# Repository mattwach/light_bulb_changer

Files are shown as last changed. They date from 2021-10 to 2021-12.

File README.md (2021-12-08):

# Light Bulb Changer

_Note: I also made a [video describing the project](https://youtu.be/A-EdzPTZSjM)._

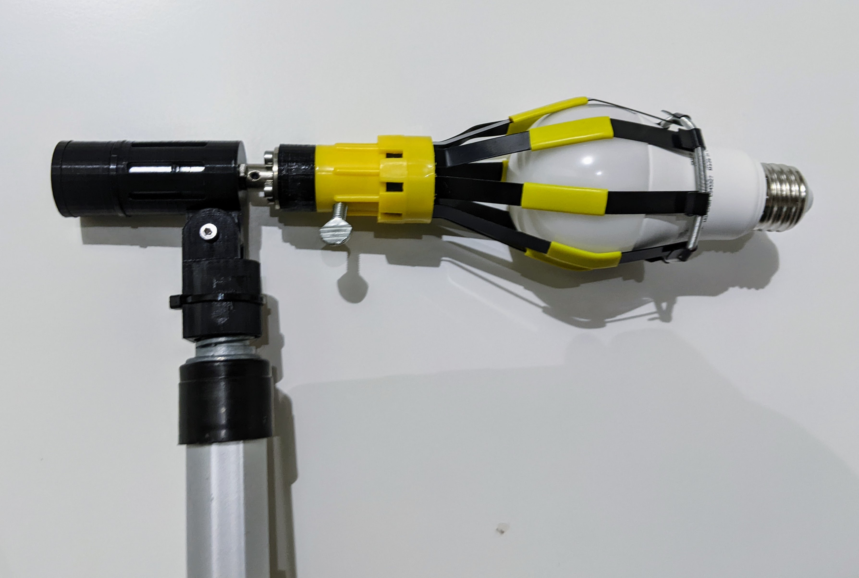
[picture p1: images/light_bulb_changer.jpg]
Light bulb changer


Do you have hard-to-reach light bulbs?  If so, then you are perhaps familiar a
_Light Bulb Changer_.  It threads on the end of a pole and extends your reach. 
A problem is one of mechanics.  If you can't get your pole square to the bulb,
the effectiveness of the holder decreases rapidly.  Imagine trying to use
this thing at a 90 degree angle to the bulb.  That is the exact situation I
found myself in: 

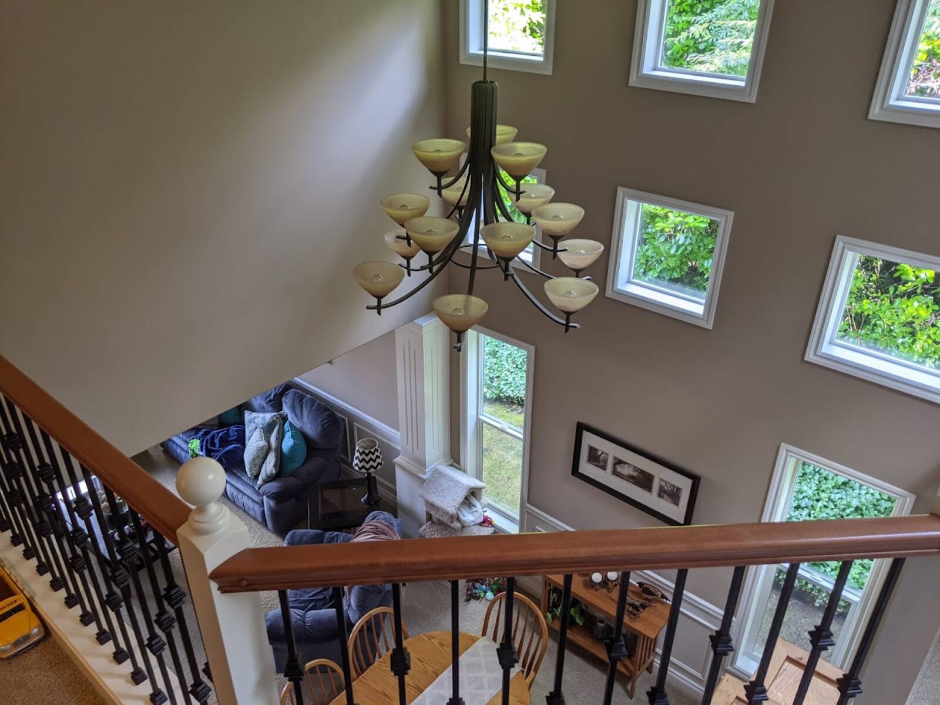
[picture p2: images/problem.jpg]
The Problem


OK. Just get a tall ladder, move that table, make that suspicious call
confirming my life insurance details and up I go.  Just kidding, I instead
used this as an excuse for another maker project.

I spent way more time on this than the ladder would have taken.  Then again, it
was quite a bit of fun and now I have a useful tool on-hand ready to square off
against the next light bulb challenge.  Lucky for you, all of the design,
modeling, and testing steps are done so you can build one in a fraction of the time.
Heck, I even include a walkthrough below.

Of course if you want extra challenge, feel free to mod up the design below to
match your favorite parts and techniques.  Have it play inspirational music, add
Bluetooth for some reason... Your imagination, skill, time and budget are your
only limits.

If you don't have a 3D printer, hope is not lost.  You can always use a project
box, parts from the hardware store and plenty of zip ties to get things done old
school.

## Step 1: Parts

Here is what I built:

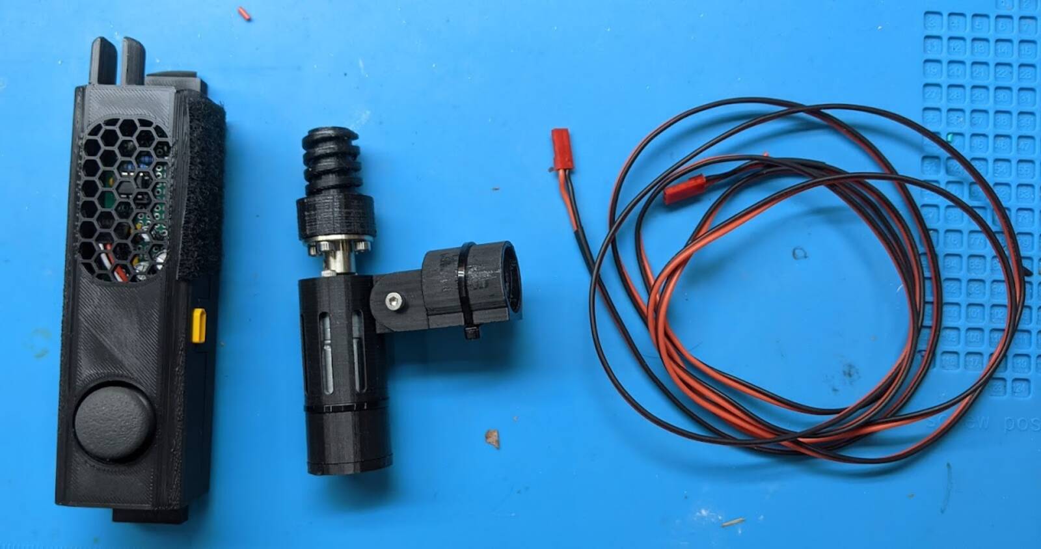
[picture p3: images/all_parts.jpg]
All of the parts


The middle unit is a motorized driver that the light bulb changer screws onto.
It then screws on a pole.  Now you have both a motor and a way to change the
angle.  There is also a control box that goes on the other end of the pole.

### Parts I used include:

   1. **[Geared brushed motor](https://www.amazon.com/gp/product/B0728HDH45)**.  These
      are around $13 on Amazon, probably cheaper other places.  I went with 200
      RPM which is a bit more than 3 rotations/second at 12V.  This seemed about
      right.
   2. **[Flange Coupling Connector](https://smile.amazon.com/gp/product/B07PDYV4P3)**. 
      This is needed to adapt the motor's shaft to the _Light Bulb Changer_.
   3. **Microcontroller**. I went with the [ATTiny85](https://www.sparkfun.com/products/9378)
      Loading firmware on it can be tricky if you have not done so before.  But there are
      dozens of video and written guides on the internet on how to do it.  Once you
      get it working the first time, it will be turn key after that.
   4. **[L293D](https://www.adafruit.com/product/807) H-bridge motor driver**.
      This turns the puny waveforms the ATTiny85 can generate into power boosted
      energy waves that can drive a motor at variable speeds and in either forward
      or reverse.
   5. **Broomstick** for mounting
   6. **[Enough wire](https://www.amazon.com/BNTECHGO-Flexible-Conductor-Resistant-Extension/dp/B077X9MVWG)**
      to reach all the way down the broomstick.
   7. **Zipties** to secure the control module to the broomstick.
   8. **[Sony PS2 thumbstick](https://www.amazon.com/HiLetgo-Controller-JoyStick-Breakout-Arduino/dp/B00P7QBGD2)**
      which is basically a thumb-friendly potentiometer. Any 10k potentiometer will work,
      so long as you can handle the ergonomics.
   9. **A power source**.  You'll need around 12V and enough current to keep the motor
      happy.  A [3S lipo battery](https://www.amazon.com/TATTU-Battery-650mAh-Torrent-Lizard/dp/B071GBGBB4)
      (450-1800 mAh) fits this bill perfectly, but you'll need a special charger if you don't already
      have one.  You can also stack 9 (or more) AA batteries in series.  A 12V DC wall wart could also work.
   10. **Connectors for the power source**.  With a small 3S LIPO, I really like
       the [XT30 connector](https://www.amazon.com/10Pairs-Upgrade-Connector-Female-Battery/dp/B08P5HVMYT)
       and that is what the 3D printed case is designed to handle without
       "manual modifications"
   11. **PCB prototyping board** - Technically optional as there are so many way to construct a circuit.
       But a [30x70 perf board](https://www.amazon.com/ELEGOO-Prototype-Soldering-Compatible-Arduino/dp/B072Z7Y19F)
       is my personal preference.
   12. **Status LED(s)**.  I went with a two-color LED which has red and green
       channels.  You can also go with two separate LEDs of any color you want with minimal changes.
   13. **Some current limiting resistors** for the LEDs.  Values are not critical -
       something in the 470 to 2k range will work.
   14. **A 5V regulator**.  I went with the LP2950Z but [nearly anything](https://www.sparkfun.com/products/107)
       will work here. 
   15. **Some capacitors**.  The DC motor is a noisy load for the battery and the 5V
       regulator will see this noise on it's input.  Caps on each side of the
       regulator will help reduce this noise to the 5V electronics  I went with
       500+ uF on the input side and another 100 uF on the output side, which is
       likely overkill.
   16. **Connectors** for the PS2 thumbstick and motor wire.  I used standard 2.54mm pitch
       headers.  Anything you have could work.

### Tools you'll need:

   1. **A 3D printer** if you want print the motor housing and controller box.  As
      said above, you can also come up with a custom alternate solution.
   2. **A Breadboard** if you want to verify operation before committing the parts with
      solder.

## Step 2: Electronics Overview

The ordering is not strict here but I like getting the electronics working
first.  A breadboard is a good way to wire things up and some confidence
that the project is on the right track.

Here is the schematic:

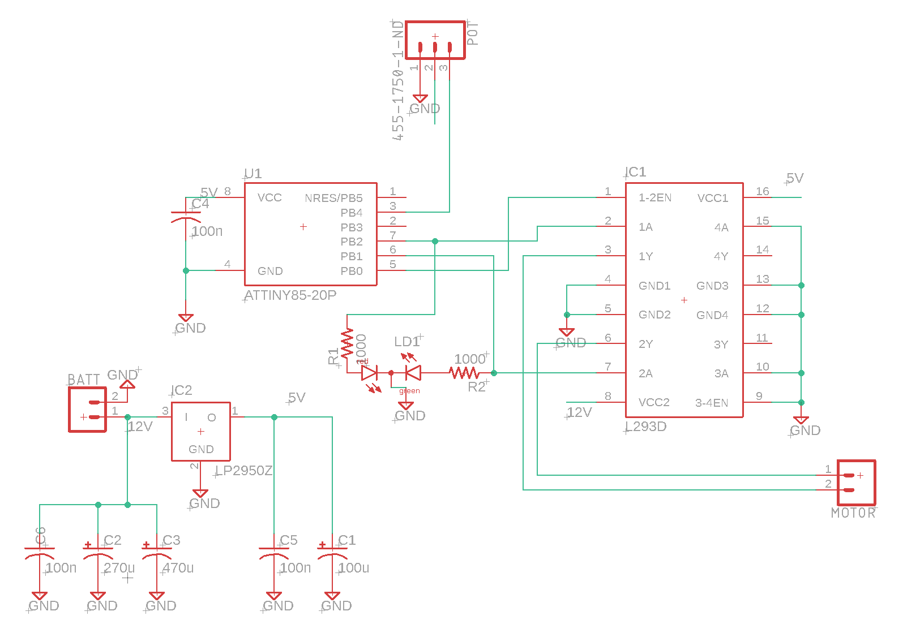
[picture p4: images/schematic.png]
Schematic


You do not need to starting wiring up the breadboard yet, as upcoming steps
will break that down into smaller steps

So how does this thing work?

   * You move the potentiometer (PS2 thumbstick, top of schematic)
   * The ATTiny85 microcontroller notes the new potentiometer state (via `PB4`)
     and uses it to update the motor direction and speed. 
   * The direction and speed are communicated via a PWM signal (via `PB0`) which
     tells the motor how fast to spin via the only language it understands: power.
     The microcontroller also sends a signal (via PB1 and PB2) that tells the motor
     controller which polarity to send to the motor.
   * The L293D motor controller (right) takes the weak PWM signal from the microcontroller and
     puts the full force of the battery pack behind it (e.g. 12V and whatever
     current the motor asks for - within obvious limits..)
   * The bottom left of the circuit is just the 5V regulator and some supporting
     capacitors to filter out motor noise.

You can probably imagine the rest - adapter on motor, light bulb changer on
adapter and light.  Turning, problems being solved, happy time.

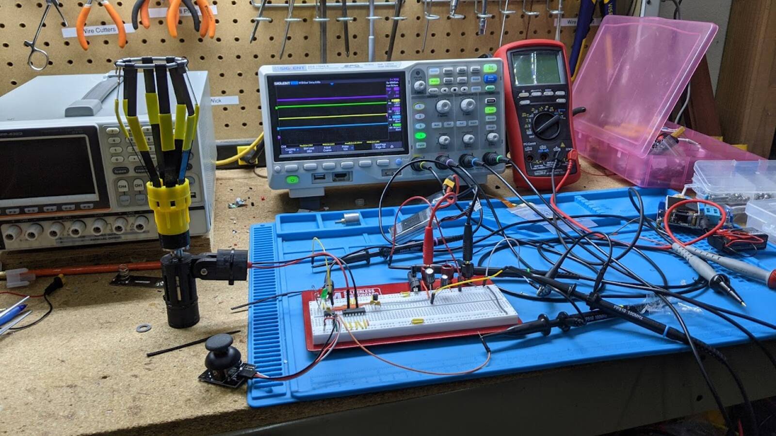
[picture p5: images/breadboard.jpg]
Breadboard


## Step 3: ATTiny85 Programming and Testing

The code is located in the `firmware/` directory.  This code is not Arduino so
you will need to have/develop familiarity with `avr-gcc` to compile it.  But,
**you don't have to compile it** because there is an already-compiled
`firmware/prebuilt/light_bulb_changer.hex` file ready to go.

Loading code onto the ATTiny85 involves conforming to the protocol specified in
its
[datasheet](https://ww1.microchip.com/downloads/en/DeviceDoc/Atmel-2586-AVR-8-bit-Microcontroller-ATtiny25-ATtiny45-ATtiny85_Datasheet.pdf).
There are several possible solutions and a large amount of websites and Youtube
videos that cover the topic.

A sampling of options include:

   1. The official AVR programming tools
   2. [Using an Arduino Uno (or nano) *as a programmer*](https://create.arduino.cc/projecthub/arjun/programming-attiny85-with-arduino-uno-afb829)
   3. [Using the Sparkfun ATTiny85 programmer](https://learn.sparkfun.com/tutorials/tiny-avr-programmer-hookup-guide/all)

I personally went with a variation of option #2, using an Arduino Nano and
a [test clip](https://www.amazon.com/Pomona-Electronics-5250-Plated-Spacing/dp/B00JJ4G13I):

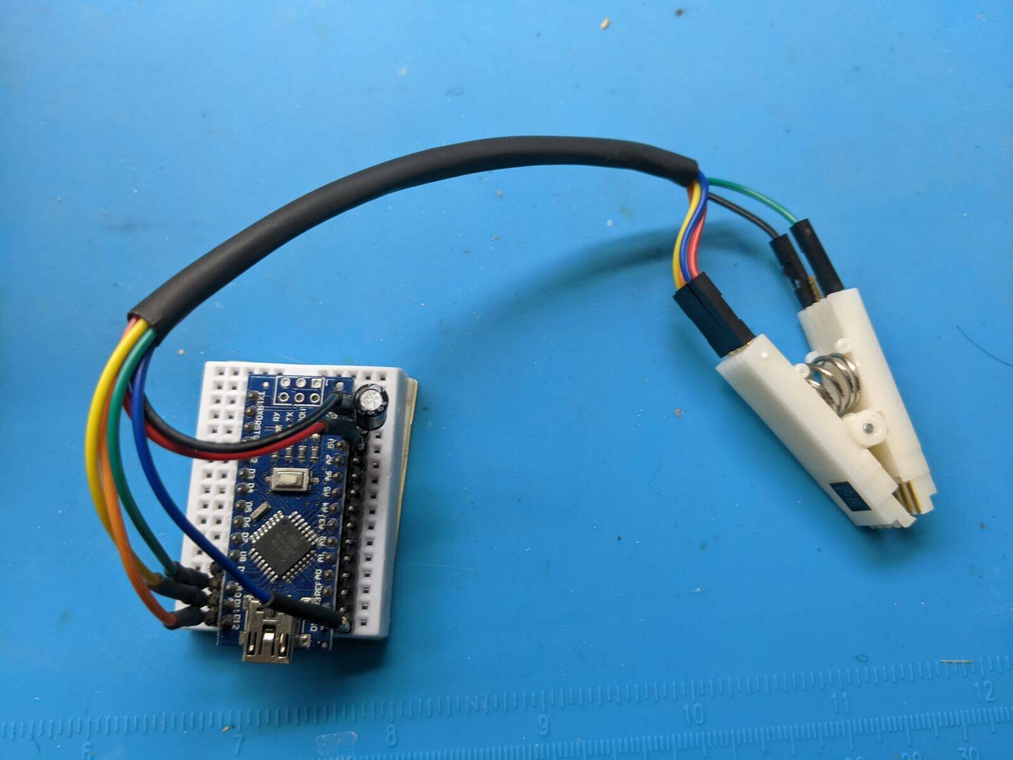
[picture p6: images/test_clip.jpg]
Test Clip


The three guides I listed above assume that you want to use the Arduino framework to
_write code_ for the ATTiny85.  Maybe you do, but Arduino can not compile the code here
and you already have a compiled `light_bulb_changer.hex` file ready to upload so compiling
it again is not needed.

Still it's convenient to follow the steps because as a part of the exercise,
you'll end up with a copy of the
[avrdude](https://www.nongnu.org/avrdude/) code uploading tool as well as
examples of how to use it.

When you run the "blinking light" example of one of the guides above, the
Arduino console will output the `avrdude` command it used.  This can be compared
to the one I used (which is also in `firmware/prebuilt/README`):

    # in the firmware/prebuilt directory:

    /usr/bin/avrdude \
      -C./avrdude.conf \
      -v \
      -pattiny85 \
      -cstk500v1 \
      -P /dev/ttyUSB0 \
      -b19200 \
      -Uflash:w:light_bulb_changer.hex:i

Depending on the programming tools you have and the OS you
are using, some flags will be different and you'll want to combine the
flags from the blinking light example with the `-Uflash:w:light_bulb_changer.hex:i`
option above.

OK, now that we are through all of that, I suggest a simple verification on the
breadboard.  We will wire up a simplified version of the schematic as shown:

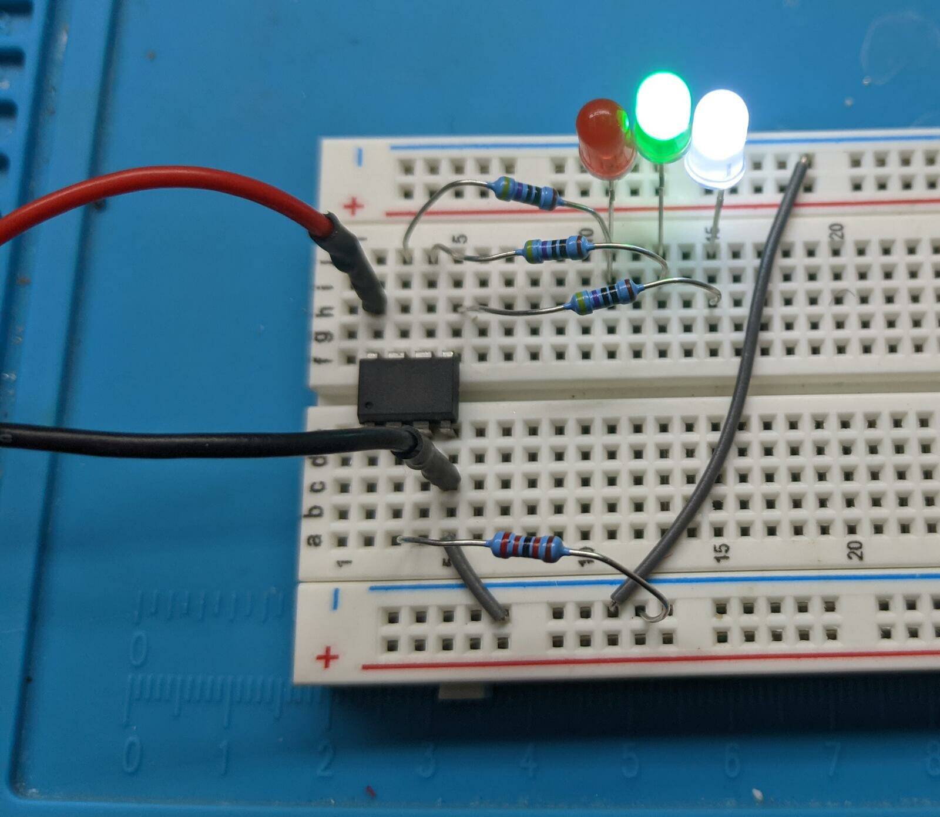
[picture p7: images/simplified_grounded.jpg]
Simplified Grounded Breadboard


This follows the original schematic but with the motor enable (pin 1 of the
    L293D) replaced with a white LED and the potentiometer replaced with a
resistor to ground.  Specifically:

   * Pin 1 (Reset) Not Connected
   * Pin 2 (Pot input) -> Resistor -> Ground
   * Pin 3 Not Connected
   * Pin 4 (`GND`) -> Ground
   * Pin 5 (`PWM`) -> Resistor -> White LED -> Ground
   * Pin 6 (Forward) -> Resistor -> Greed LED -> Ground
   * Pin 7 (Reverse) -> Resistor -> Red LED -> Ground
   * Pin 8 (5V) -> Some voltage between 2V-5.5V

What resistor values?  Anything in the 400-5K range is fine for the LEDs.
Anything at all is fine for Pin 2.

What we should see is the green and white LEDs lit up.  The firmware thinks that
the motor is in full-power forward mode because we have Pin 2 grounded.

Now lets, make one change.  Instead of grounding Pin 2, connect it to power:

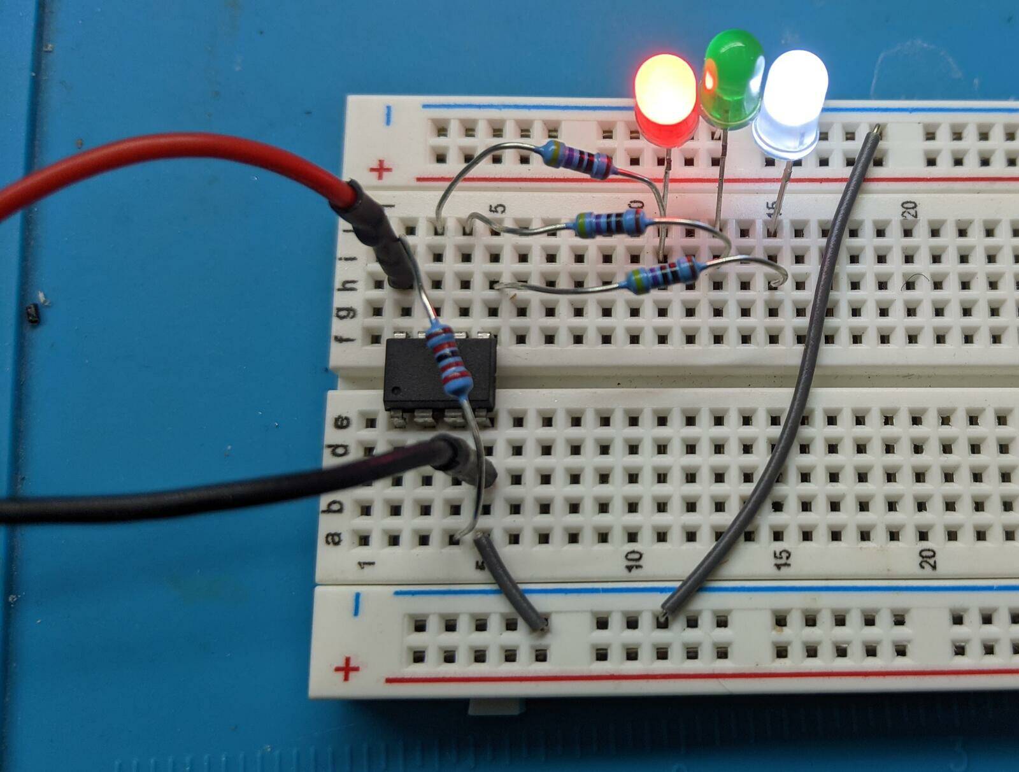
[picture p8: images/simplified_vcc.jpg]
Simplified VCC Breadboard


Now the ATTiny85 thinks it need to drive the motor full power in reverse.

You could call the testing "done" at this point, but I'm going to take it a
little further for educational purposes.  Here I connected a real potentiometer
to pin 2 (I didn't go with the PS2 thumbstick just yet because I wanted to
    potentiometer to stay at a certain value for the test).  I also added
an oscilloscope probe to pin 5:

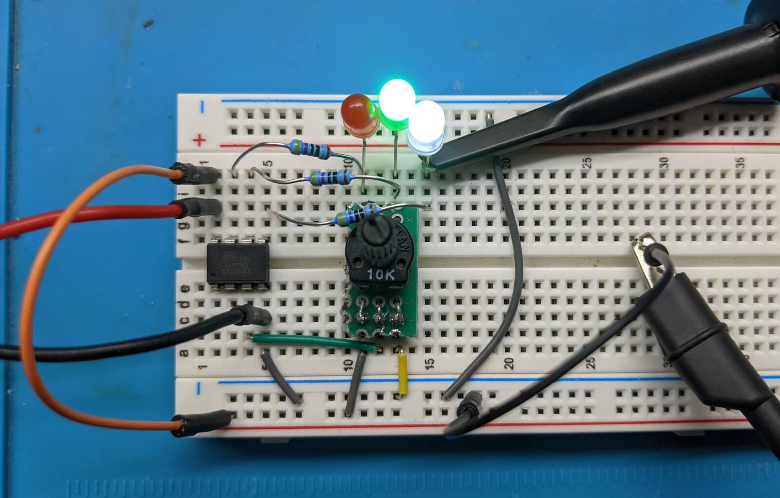
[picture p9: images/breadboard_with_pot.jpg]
Breadboard with Potentiometer


Now the potentiometer can be used to change between forward and reverse, just
like the final product.  It's also possible to see the white LED getting
darker and brighter but this is more obvious from the oscilloscope.  Here
is a scope image at "low power", where the motor will turn more slowly.  Note
how the signal spends most of it's time at 0V:

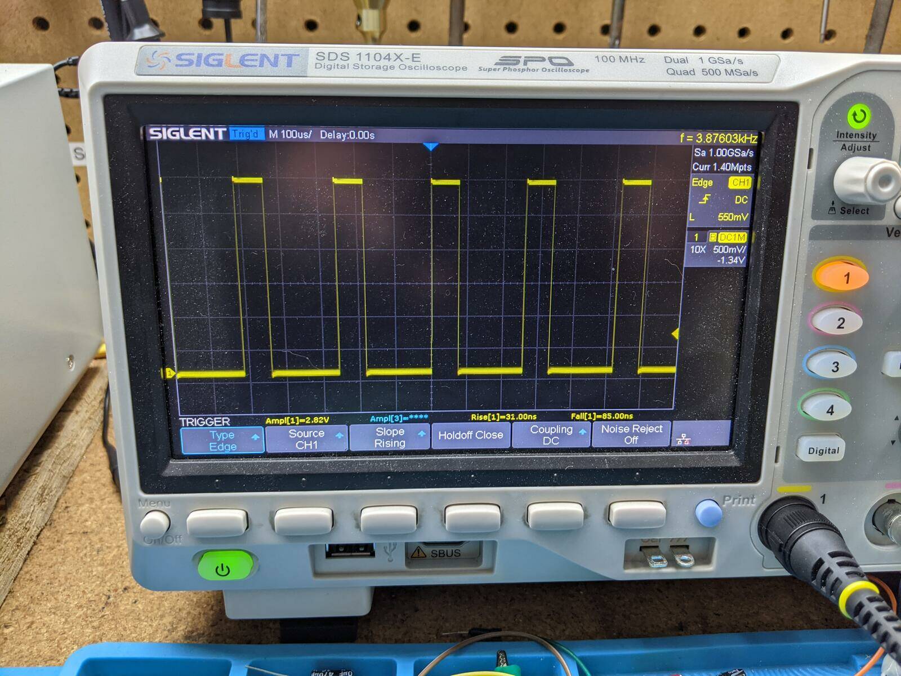
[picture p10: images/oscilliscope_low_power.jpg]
Oscilloscope Low Power


Here, the potentiometer is turned further to the left (or right since there
is both a forward and reverse).  More time at 5V means more motor speed:

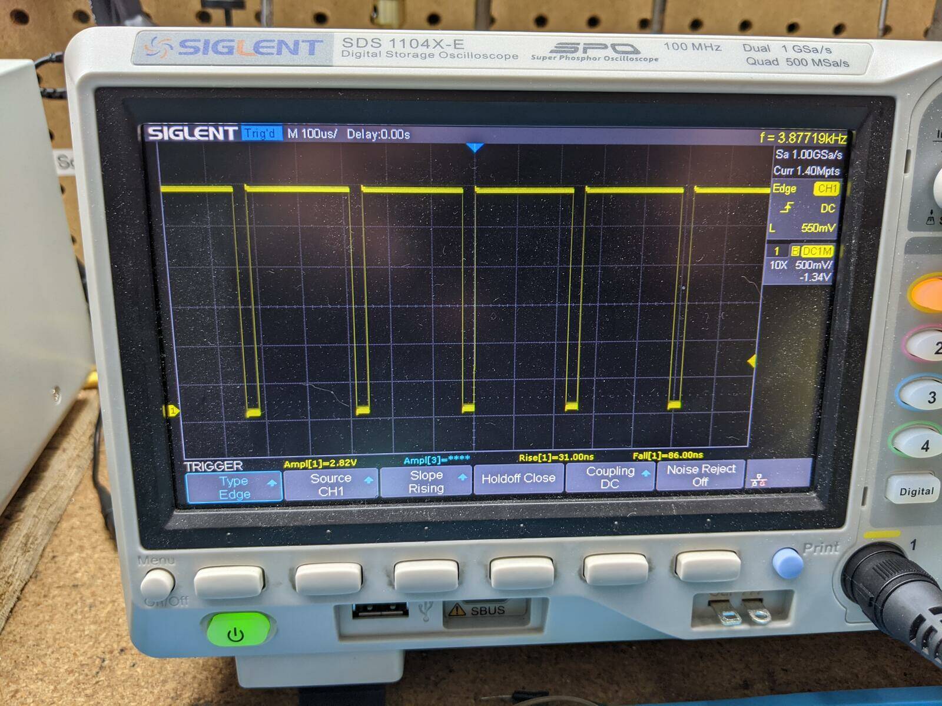
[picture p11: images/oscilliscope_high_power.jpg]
Oscilloscope Low Power


and finally, the highest power setting shows the signal at 5V the whole time:

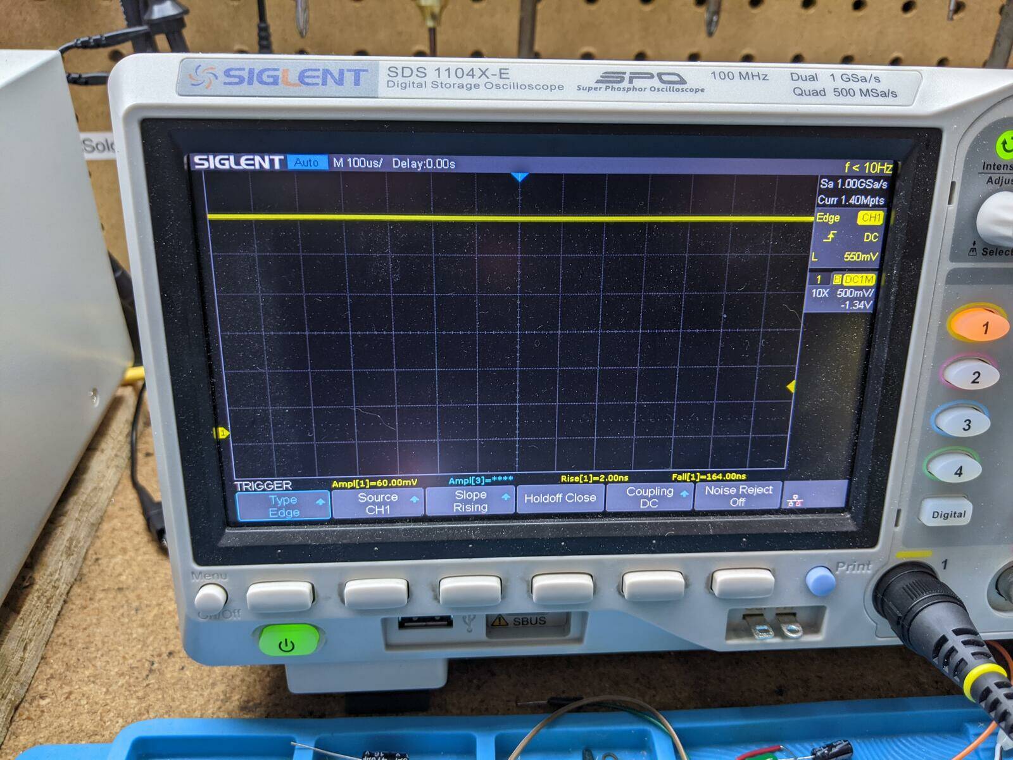
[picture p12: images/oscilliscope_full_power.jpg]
Oscilloscope Low Power


## Step 4: Building the PCB

Repeating the schematic:

Schematic

Here is a board layout that represent my own strategy for building the PCB:

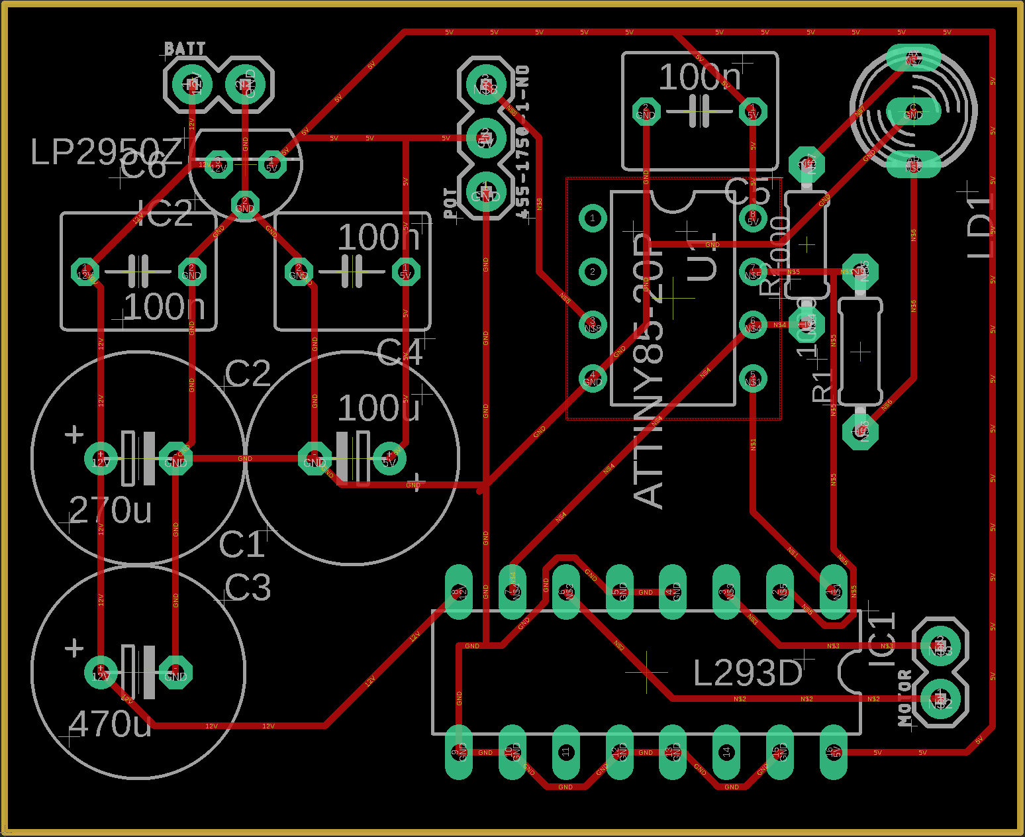
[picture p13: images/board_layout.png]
Board Layout


Actual built-up part:

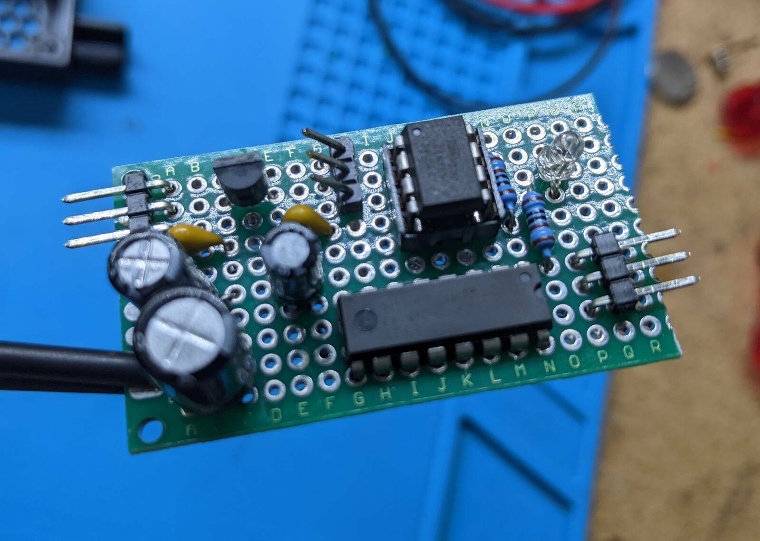
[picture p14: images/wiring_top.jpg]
Board Top


Of course, you can build the board any way you want.  Just keep in mind that
the 3D printed control box is sized to house a PCB that is 30mm x 51mm.  This
size could (technically) be changed in the `3d_print/motor_controller_pcb.scad`
file by someone who is willing to do some OpenSCAD work.
 
## Step 5: 3D Print Control Box and Motor Carriage

There are two directories of interest.  

The one named `stl/` contains already-rendered parts.

The other one is named `openscad/`.  If
you just want the parts, _you can ignore this directory_.  If you want to
customize the parts, you'll need the (free) OpenSCAD software.  The main
files of interest are `openscad/control_box_assembly.scad` and
`openscad/motor_assembly.scad`.  Scroll to the bottom of each file
and note the comments.

Here is a inventory of each part:

Starting with the motor box, we have a threaded interface to the light
bulb removal tool (`threaded_attachment.stl`):

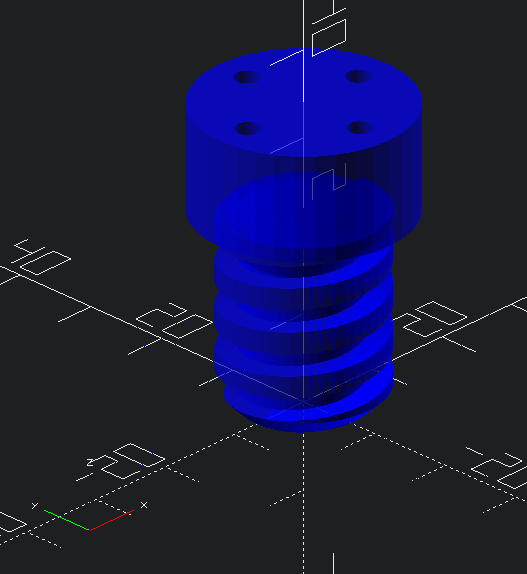
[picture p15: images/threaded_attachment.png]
Threaded Attachment


Next, the carriage for the motor (`motor_carriage.stl`):

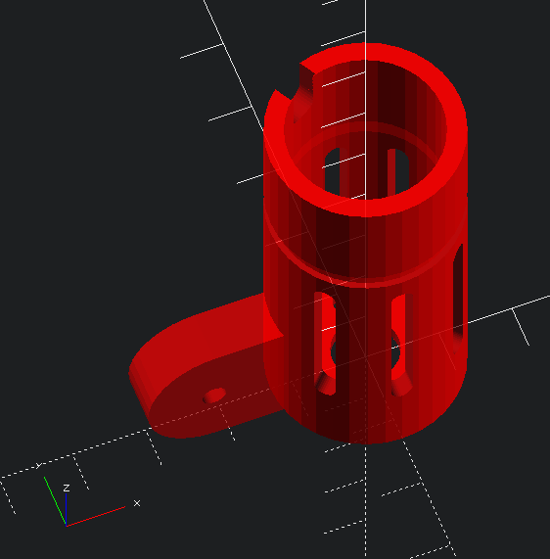
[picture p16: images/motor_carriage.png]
Motor Carriage


And a cover for the motor carriage (`motor_carriage_cover.stl`):

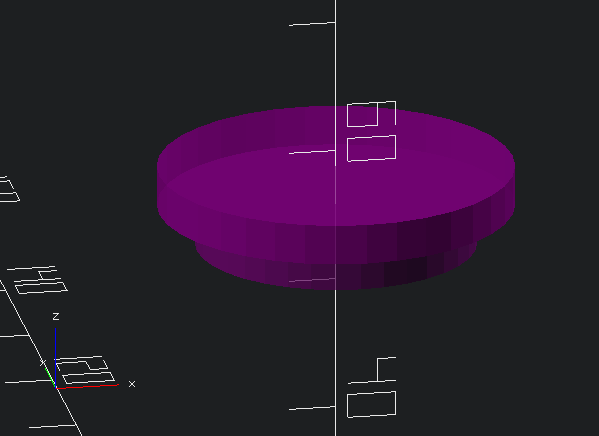
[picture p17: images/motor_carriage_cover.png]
Motor Carriage


And finally an interface between the motor carriage and pole (`pole_interface.stl`) 

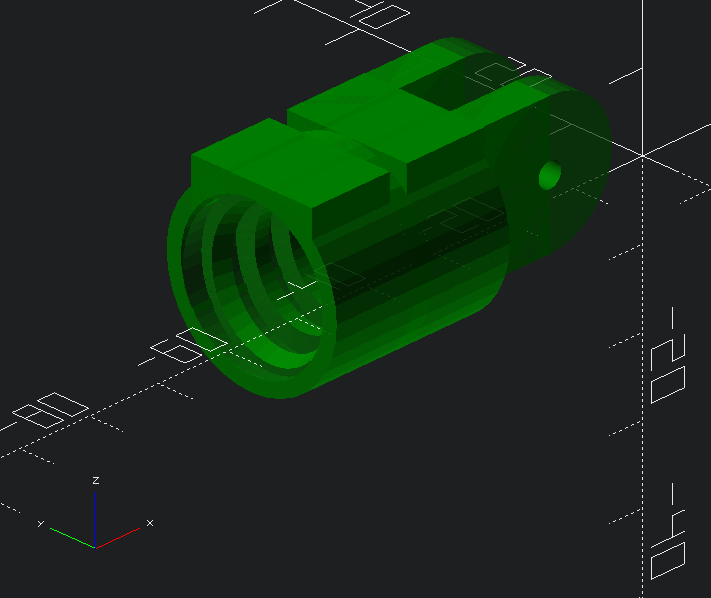
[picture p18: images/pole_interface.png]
Pole Interface


Onto the control box.  This consists of three components held together by 16mm
M3 bolts.  First the pole interface, which is intended to be held on with
zip ties (`control_box_interface.stl`):

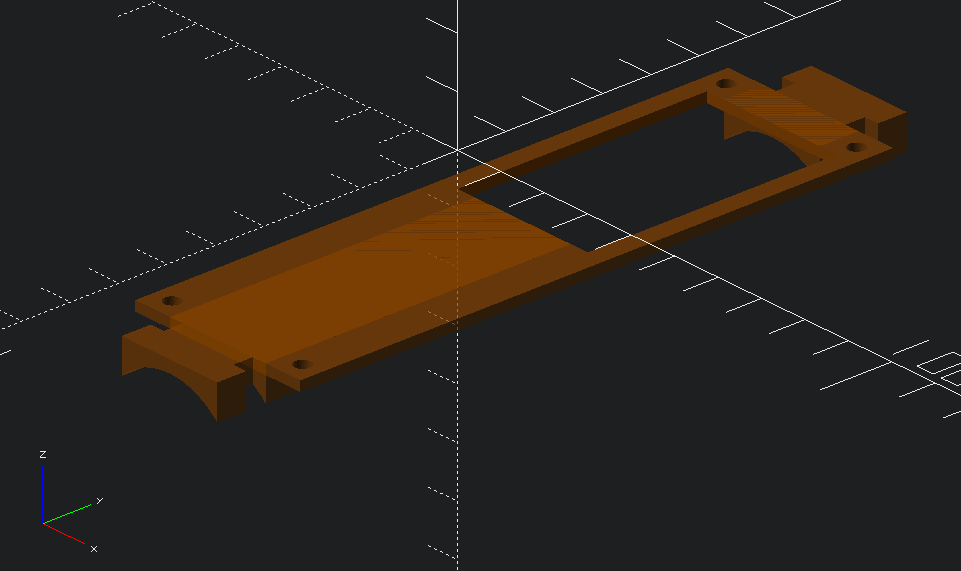
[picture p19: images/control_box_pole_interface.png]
Control Box Pole Interface


Next, the middle section, which holds all of the electronics (`control_box_bottom.stl`):

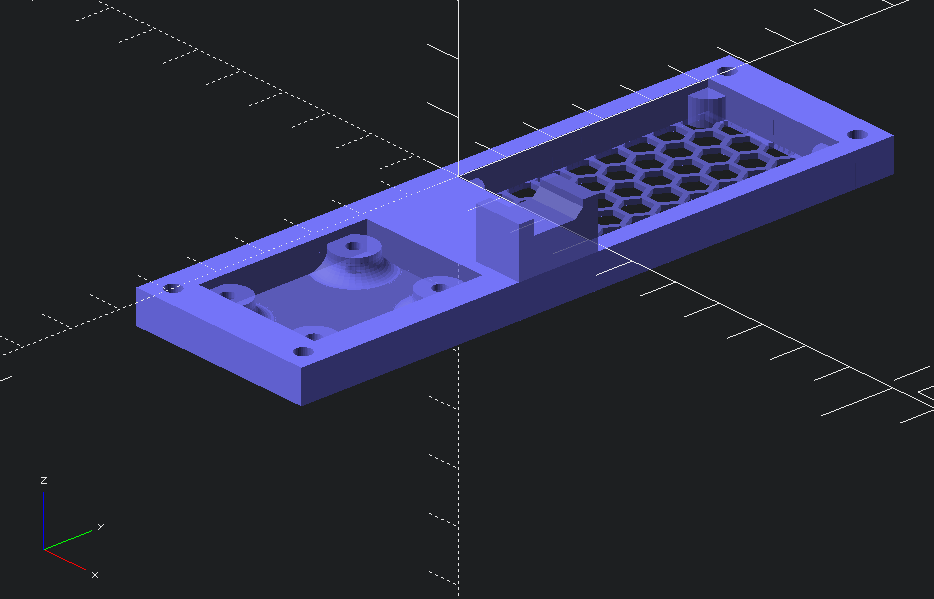
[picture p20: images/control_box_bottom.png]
Control Box Pole Interface


And finally the top cover (`control_box_top.stl`):

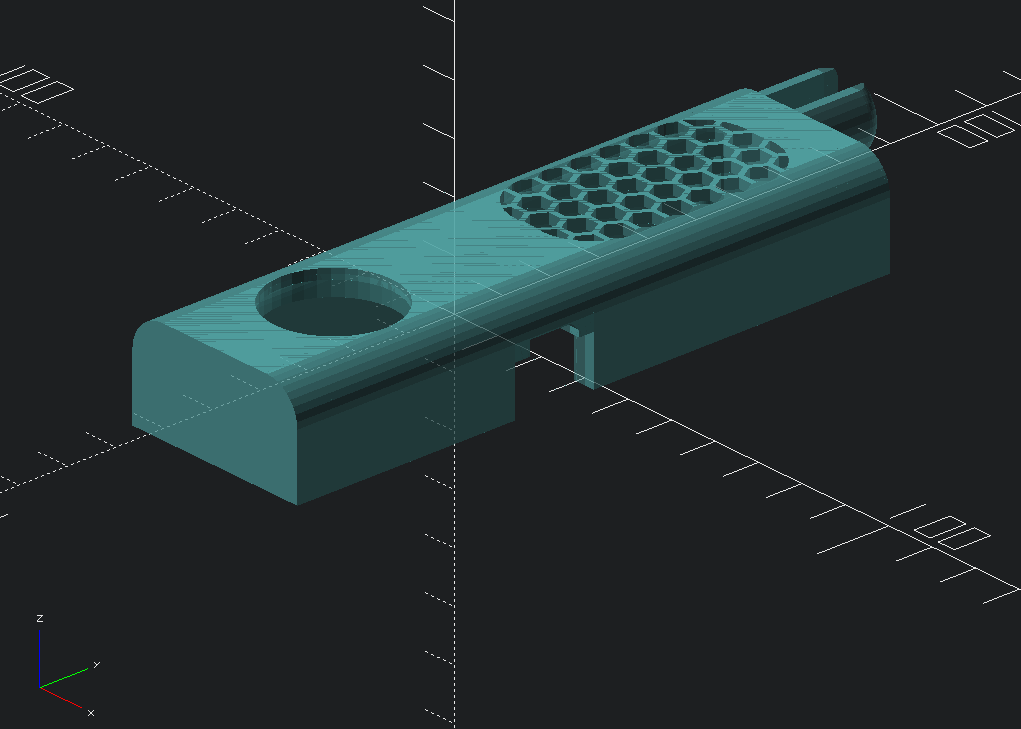
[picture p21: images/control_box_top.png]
Control Box Top


Here is everything assembled:

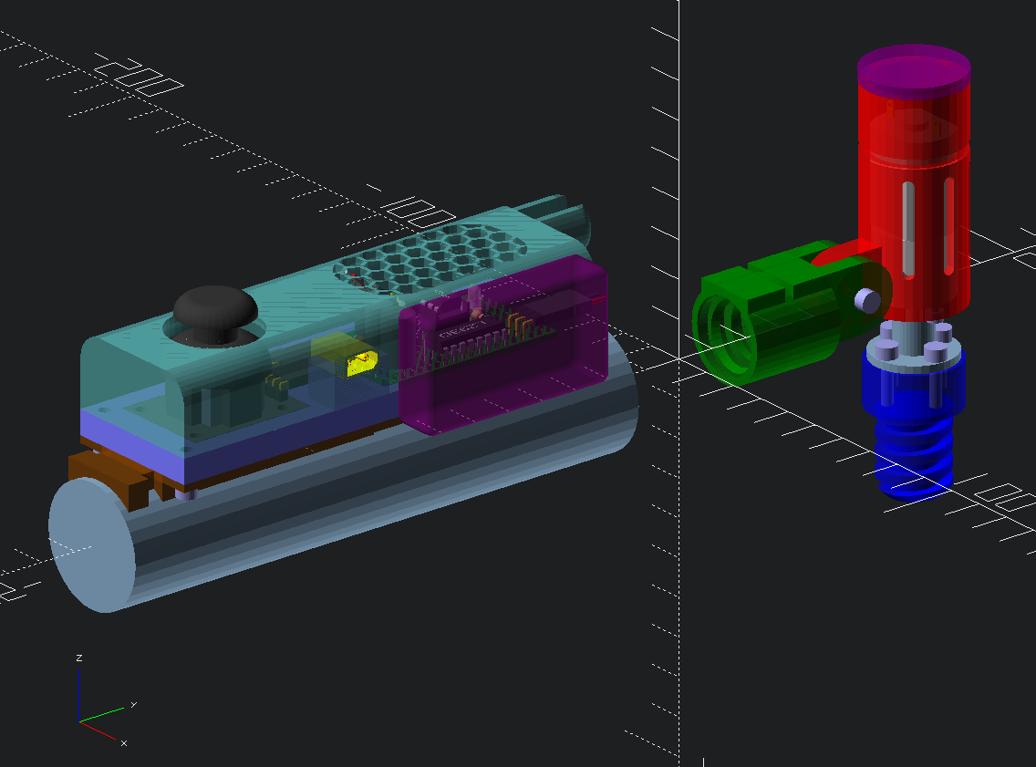
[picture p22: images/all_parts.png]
All Parts


## Step 6: Final Assembly

Here is an rendered and actual image of the control box assembly.  Refer to the
previous steps for more details on the electrical connections.

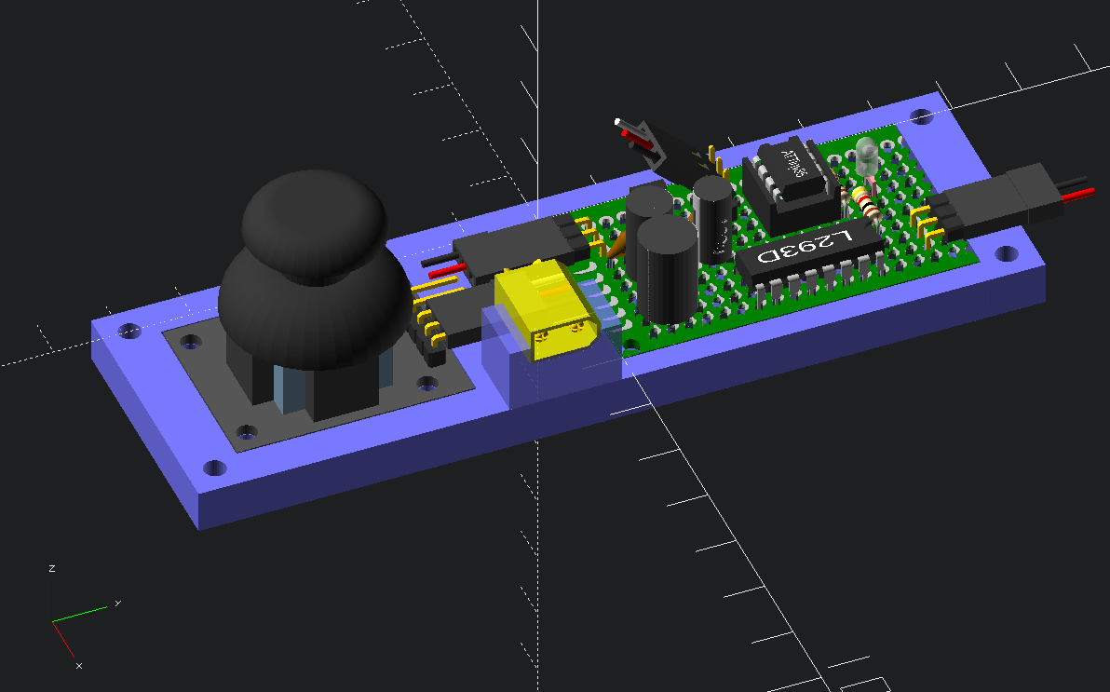
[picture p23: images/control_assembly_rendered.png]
Control Assembly Rendered


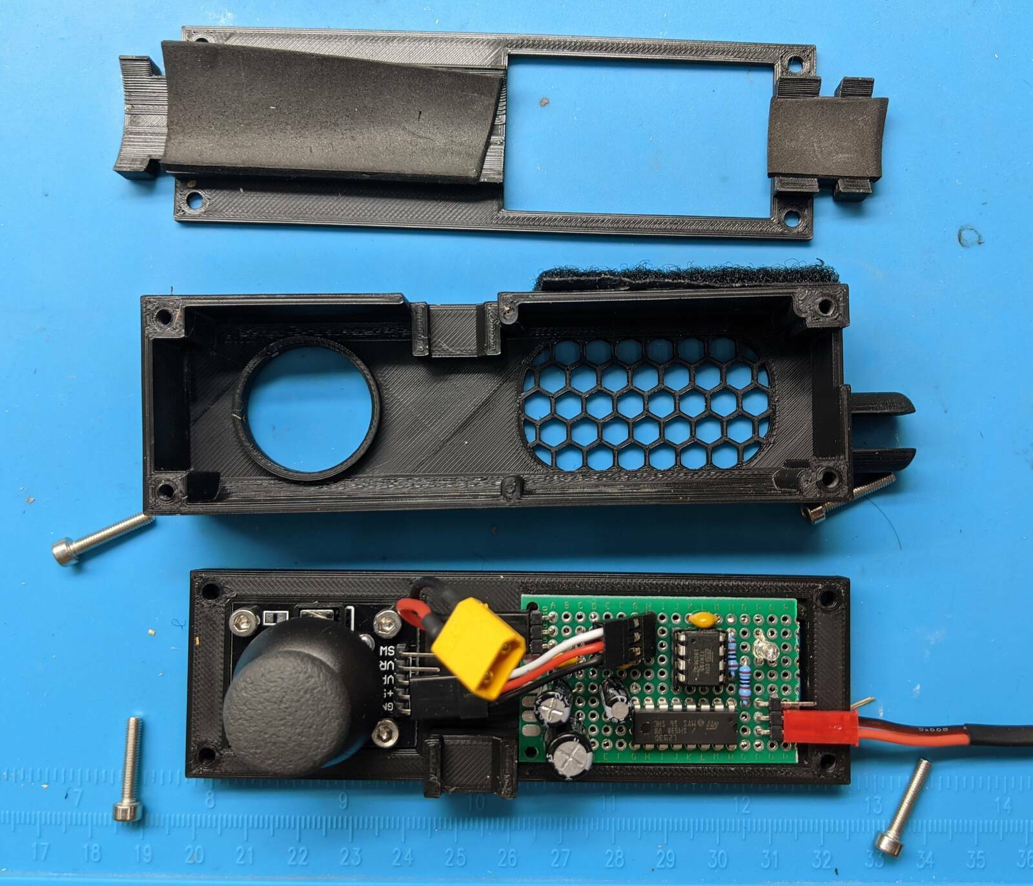
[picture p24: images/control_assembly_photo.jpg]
Control Assembly Photo


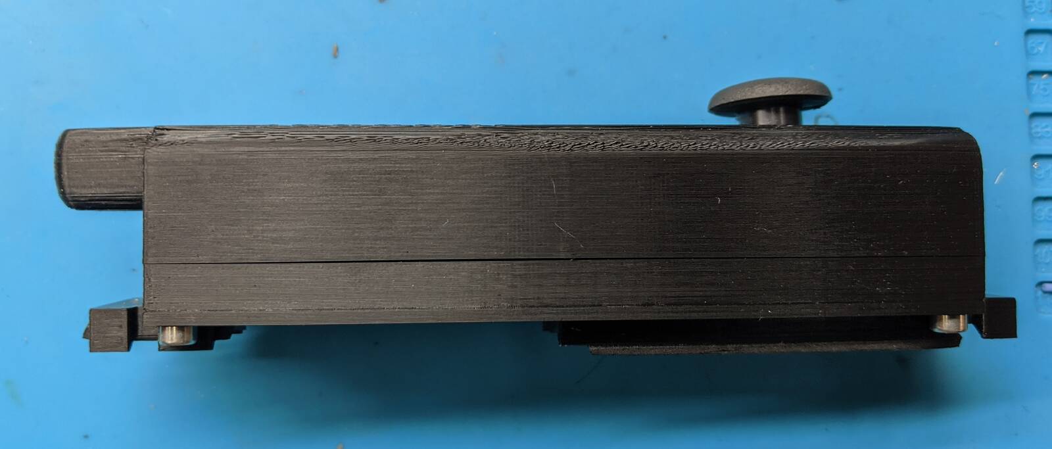
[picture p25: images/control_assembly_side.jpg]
Control Assembly Side


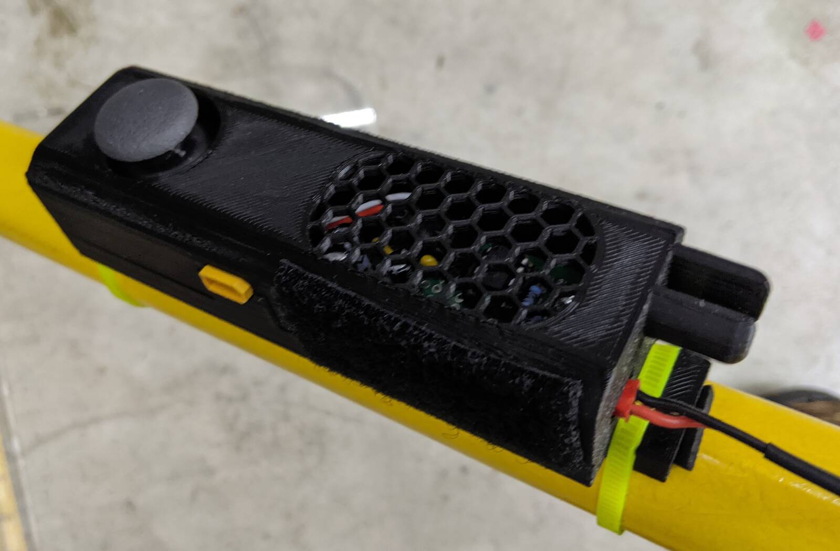
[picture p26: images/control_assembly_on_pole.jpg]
Control Assembly On Pole


Here are some images to show how the motor assembly is supposed to work:

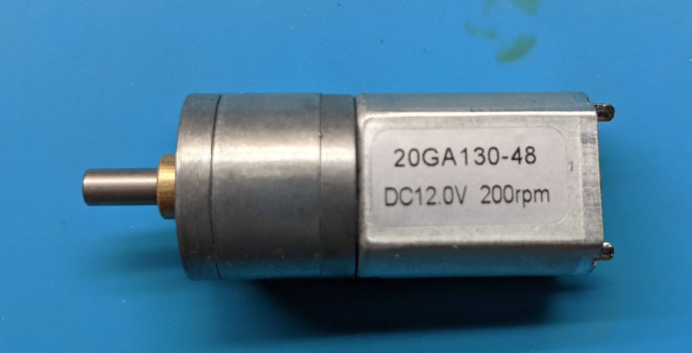
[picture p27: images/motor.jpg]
Motor


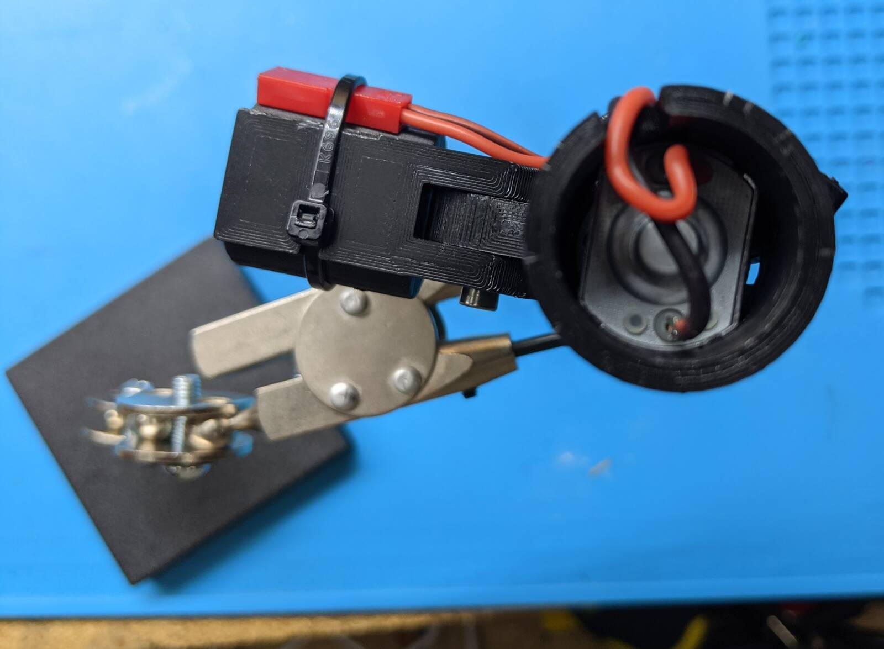
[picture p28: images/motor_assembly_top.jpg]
Motor Assembly Top


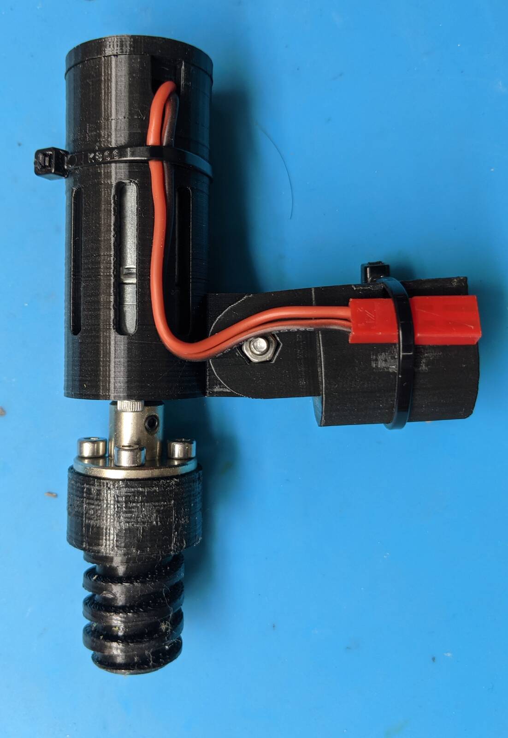
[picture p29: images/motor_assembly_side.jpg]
Motor Assembly Side


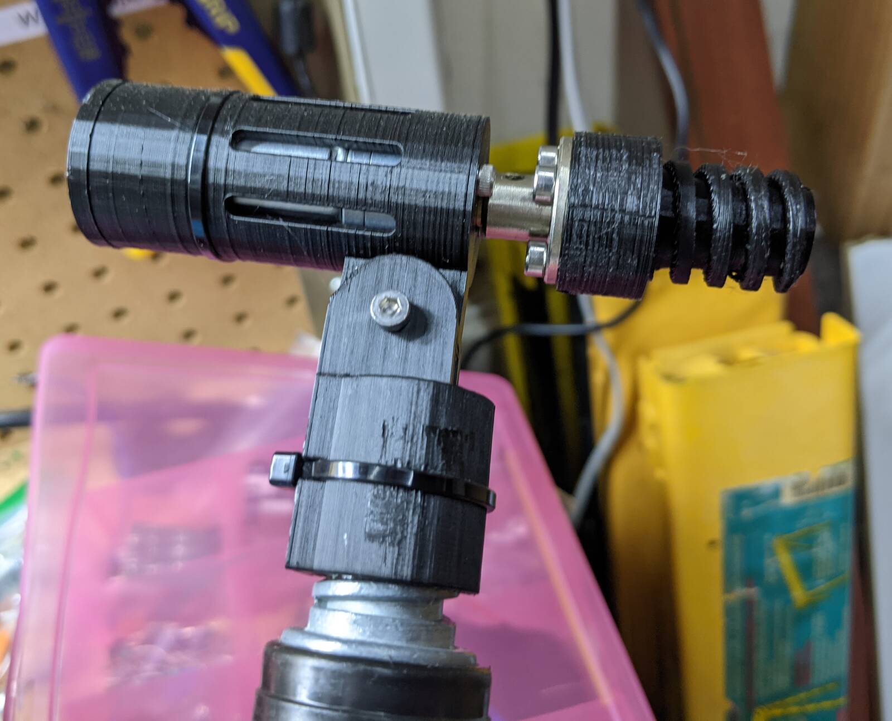
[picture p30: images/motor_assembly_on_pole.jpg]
Motor Assembly On Pole


Note that if the motor is spinning the wrong way, you can just reverse the
motor connection at the control box (NOT the battery connection).

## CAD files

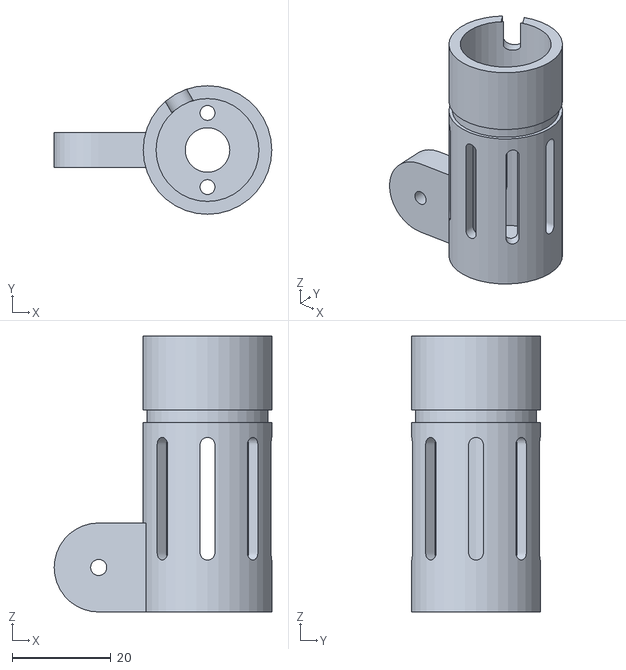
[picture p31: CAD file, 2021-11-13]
stl/motor_carriage.stl
44.0 x 26.0 x 55.8

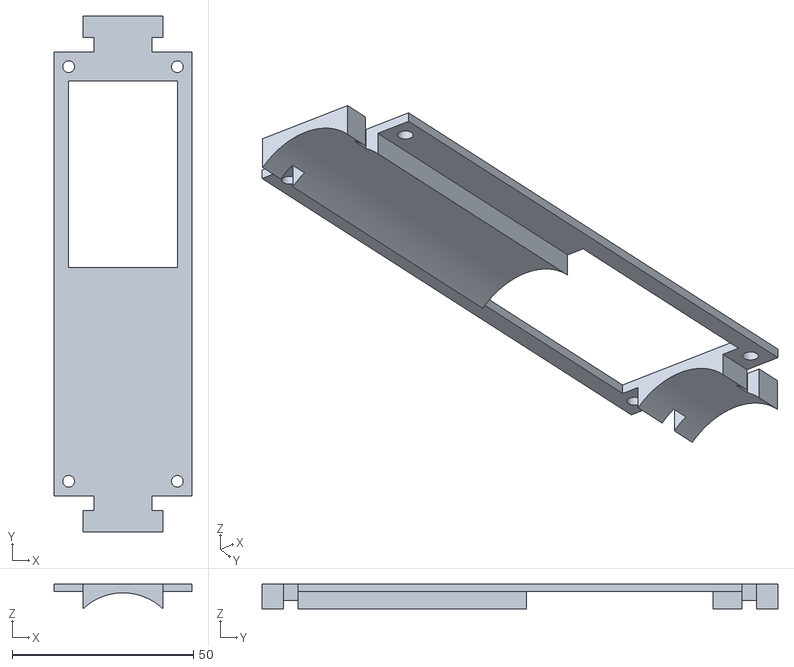
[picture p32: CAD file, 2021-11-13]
stl/control_box_pole_interface.stl
38.0 x 142.5 x 6.78

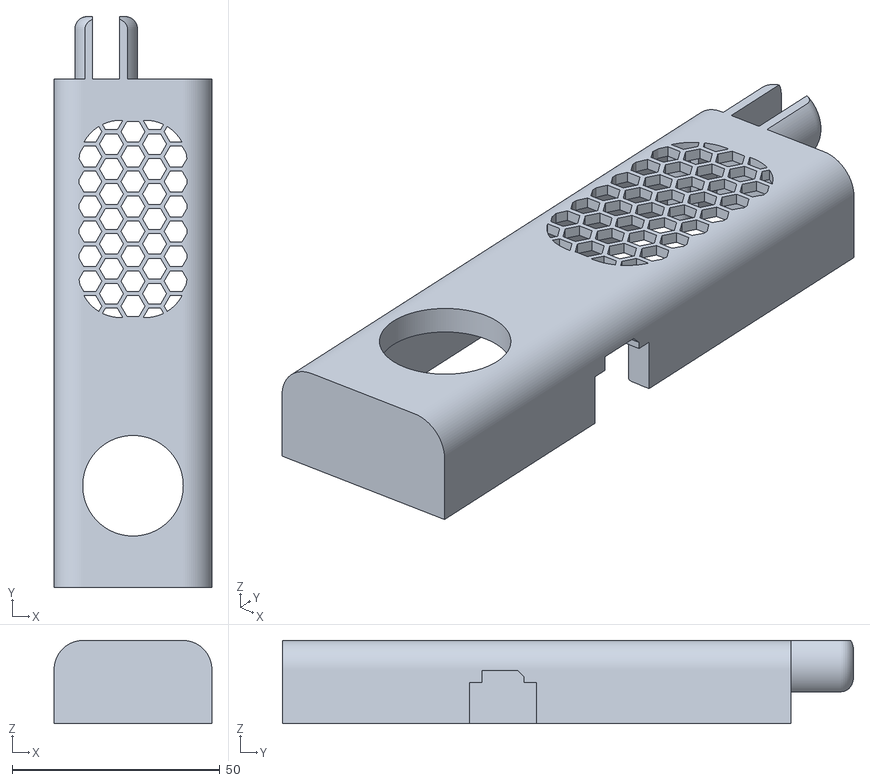
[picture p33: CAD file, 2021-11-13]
stl/control_box_top.stl
38.0 x 137.5 x 20.0

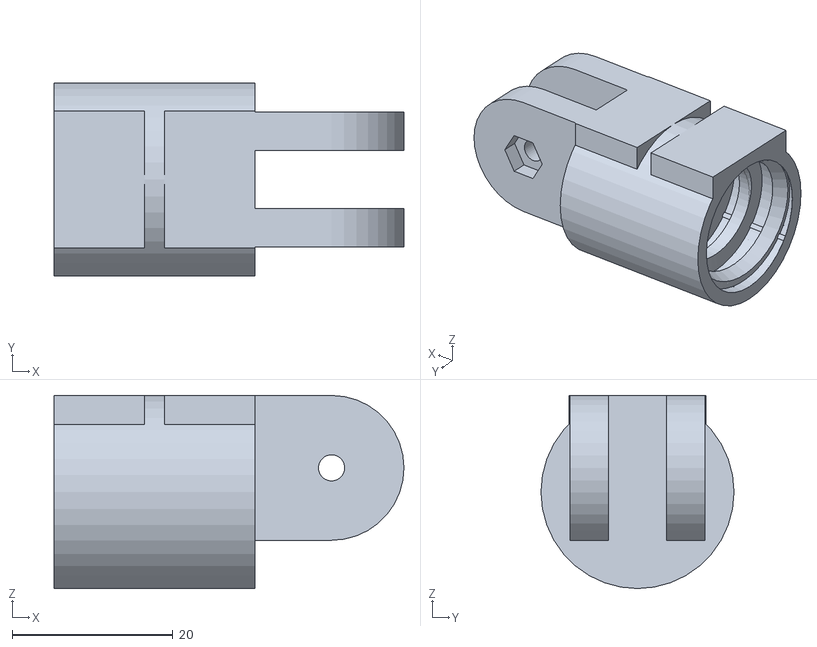
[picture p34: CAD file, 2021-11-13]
stl/pole_interface.stl
43.5 x 24.0 x 24.0

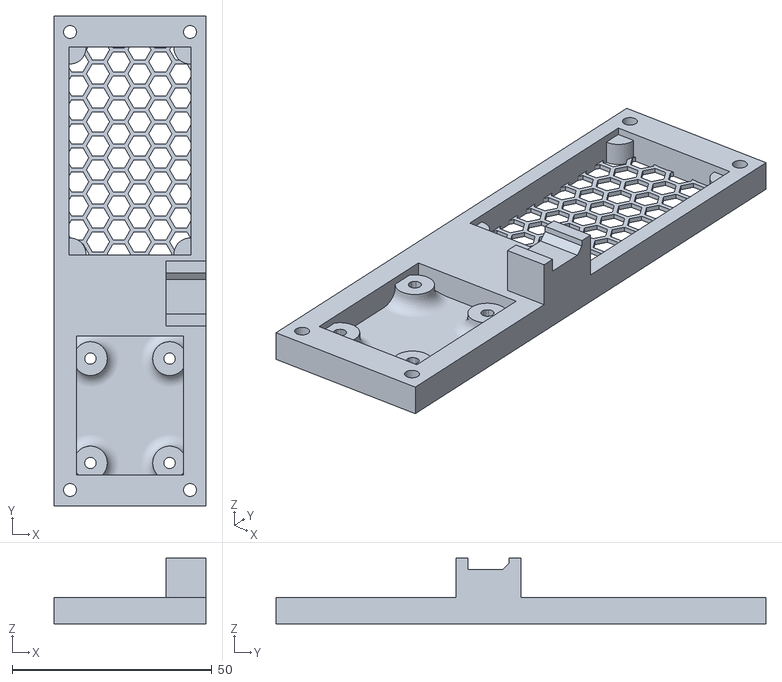
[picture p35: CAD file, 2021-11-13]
stl/control_box_bottom.stl
38.0 x 122.5 x 16.5

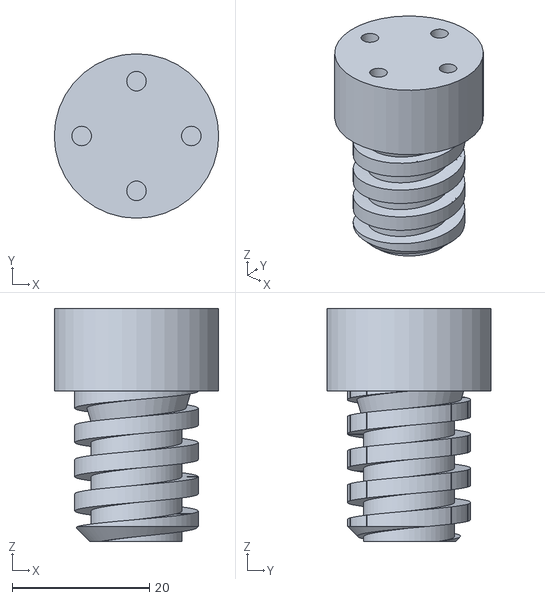
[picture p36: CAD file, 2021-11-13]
stl/threaded_attachment.stl
24.0 x 24.0 x 34.0

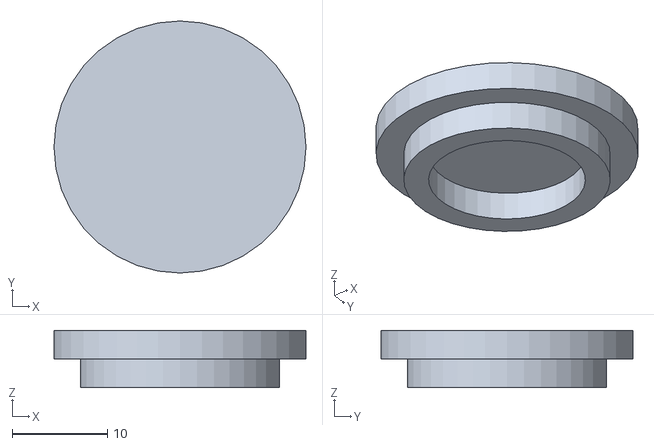
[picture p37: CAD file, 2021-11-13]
stl/motor_carriage_cover.stl
26.4 x 26.4 x 6.00

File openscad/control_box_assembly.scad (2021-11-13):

use <lib/mattwach/util.scad>
use <lib/mattwach/shapes.scad>
use <lib/mattwach/honeycomb.scad>
use <lib/mattwach/vitamins/bolts.scad>
include <lib/mattwach/vitamins/rc/ps2_analog_stick.scad>
include <lib/mattwach/vitamins/rc/female_servo_connector.scad>
include <lib/mattwach/vitamins/rc/xt30.scad>
include <motor_controller_pcb.scad>

module control_box_assembly() {
  ps2_analog_stick_y = -55;
  pin_spacing = 2.54;
  xoffset = 8.73;
  yoffset = 5.87;
  overlap = 0.01;
  control_box_left_border = 4;
  control_box_right_border = 4;
  control_box_back_border = 8;
  control_box_front_border = 8;
  control_box_width = MOTOR_CONTROLLER_PCB_WIDTH + control_box_left_border +
    control_box_right_border;
  control_box_length = -ps2_analog_stick_y + MOTOR_CONTROLLER_PCB_LENGTH +
    control_box_back_border + control_box_front_border;
  control_box_base_to_pcb = 5;
  control_box_bottom_pad = 1;
  control_box_height = control_box_base_to_pcb + MOTOR_CONTROLLER_PCB_HEIGHT;
  pole_interface_thickness = 2;
  assembly_bolt_hole_diameter = 3.25;

  xt30_xdepth = 10;
  xt30_ypad = 3;
  xt30_y = -15;
  xt30_z = 7;

  bolt_inset = 4;
  bolt_centers = [
    [-control_box_left_border + bolt_inset, ps2_analog_stick_y - control_box_back_border + bolt_inset],
    [-control_box_left_border + bolt_inset, MOTOR_CONTROLLER_PCB_LENGTH + control_box_front_border - bolt_inset],
    [-control_box_left_border + control_box_width - bolt_inset, ps2_analog_stick_y - control_box_back_border + bolt_inset],
    [-control_box_left_border + control_box_width - bolt_inset, MOTOR_CONTROLLER_PCB_LENGTH + control_box_front_border - bolt_inset]
  ];

  module assembly_bolts() {
    for (i = [0:3]) {
      translate([
          bolt_centers[i][0],
          bolt_centers[i][1],
          -control_box_height - pole_interface_thickness,
      ]) rx(180) bolt_M3(16); 
    }
  }

  module pole_interface() {
    module interface() {
      pole_meet_thickness = 10;
      pole_meet_width = control_box_width - (bolt_inset + 4) * 2;
      ziptie_overhang = 10;
      ziptie_width = 4;
      ziptie_inset = 3;

      module ziptie_cutout_pair() {
        module ziptie_cutout() {
          cube([
              ziptie_inset,
              ziptie_width,
              pole_meet_thickness + overlap * 2
          ]);
        }

        tx((control_box_width - pole_meet_width) / 2 - overlap) ziptie_cutout();
        tx((control_box_width + pole_meet_width) / 2 - ziptie_inset + overlap) ziptie_cutout();
      }

      tz(-pole_interface_thickness) difference() {
        union() {
          cube([control_box_width, control_box_length, pole_interface_thickness]);
          translate([
              bolt_inset + 4,
              -ziptie_overhang,
              -pole_meet_thickness + pole_interface_thickness - overlap
          ]) cube([
            pole_meet_width,
            control_box_length + ziptie_overhang * 2,
            pole_meet_thickness + overlap
          ]);
        }
        translate([
            control_box_left_border,
            -ps2_analog_stick_y + control_box_back_border,
            -overlap-pole_meet_thickness
        ]) cube([
            MOTOR_CONTROLLER_PCB_WIDTH,
            MOTOR_CONTROLLER_PCB_LENGTH,
            pole_interface_thickness + overlap * 2 + pole_meet_thickness]);
        tz(-pole_meet_thickness + pole_interface_thickness) {
          ty(-ziptie_width) ziptie_cutout_pair();
          ty(control_box_length) ziptie_cutout_pair();
        }
      }
    }

    color("#840", 0.7) difference() {
      translate([
          -control_box_left_border,
          ps2_analog_stick_y - control_box_back_border,
          -control_box_height
      ]) {
        interface();
      }
      for (i = [0:3]) {
        translate([
          bolt_centers[i][0],
          bolt_centers[i][1],
          -control_box_height - pole_interface_thickness - overlap,
        ]) cylinder(d=assembly_bolt_hole_diameter, h=pole_interface_thickness + overlap * 2);
      }
      pole();
    }
  }

  module control_box_bottom() {
    board_spacing = 0.2;

    module main_body() {
      module xt30_bottom_support() {
        translate([
            control_box_width - control_box_left_border - xt30_xdepth,
            xt30_y,
            -overlap
        ]) difference() {
          ty(-xt30_ypad) cube([
              xt30_xdepth,
              XT30_WIDTH + xt30_ypad * 2,
              xt30_z + overlap + XT30_HEIGHT / 2
          ]);
          translate([-overlap, 0, xt30_z]) rotate([90, 0, 90]) xt30_hull();
        }
      }

      union() {
        translate([
            -control_box_left_border,
            ps2_analog_stick_y - control_box_back_border,
            - MOTOR_CONTROLLER_PCB_HEIGHT - control_box_base_to_pcb
        ]) cube([
          control_box_width,
          control_box_length,
          control_box_base_to_pcb + MOTOR_CONTROLLER_PCB_HEIGHT
        ]);
        xt30_bottom_support();
      }
    }

    module ps2_cutout() {
      hole_diameter=2.85;
      module post() {
        pad = 2.8;
        translate([0, 0, -overlap]) rounded_cylinder(
            d=hole_diameter + pad * 2,
            h=control_box_base_to_pcb + overlap - control_box_bottom_pad,
            fillet=-3);
      }

      module hole() {
        translate([0, 0, - control_box_bottom_pad - overlap * 2]) cylinder(
            d=hole_diameter, h=control_box_base_to_pcb + overlap * 4);
      }

      translate([
          (MOTOR_CONTROLLER_PCB_WIDTH - PS2_ANALOG_STICK_WIDTH) / 2,
          ps2_analog_stick_y,
          -MOTOR_CONTROLLER_PCB_HEIGHT - control_box_base_to_pcb +
              control_box_bottom_pad
      ]) union() {
        difference() {
          txy(-board_spacing, -board_spacing) cube([
              PS2_ANALOG_STICK_WIDTH + board_spacing * 2,
              PS2_ANALOG_STICK_LENGTH + board_spacing * 2,
              control_box_base_to_pcb + MOTOR_CONTROLLER_PCB_HEIGHT]);
          txy(
              (PS2_ANALOG_STICK_WIDTH - PS2_ANALOG_STICK_HOLE_SPACING_Y) / 2,
              PS2_ANALOG_STICK_HOLE_OFFSET_X) post();
          txy(
              (PS2_ANALOG_STICK_WIDTH + PS2_ANALOG_STICK_HOLE_SPACING_Y) / 2,
              PS2_ANALOG_STICK_HOLE_OFFSET_X) post();
          txy(
              (PS2_ANALOG_STICK_WIDTH - PS2_ANALOG_STICK_HOLE_SPACING_Y) / 2,
              PS2_ANALOG_STICK_HOLE_OFFSET_X + PS2_ANALOG_STICK_HOLE_SPACING_X
          ) post();
          txy(
              (PS2_ANALOG_STICK_WIDTH + PS2_ANALOG_STICK_HOLE_SPACING_Y) / 2,
              PS2_ANALOG_STICK_HOLE_OFFSET_X + PS2_ANALOG_STICK_HOLE_SPACING_X
          ) post();
        }
        txy(
            (PS2_ANALOG_STICK_WIDTH - PS2_ANALOG_STICK_HOLE_SPACING_Y) / 2,
            PS2_ANALOG_STICK_HOLE_OFFSET_X) hole();
        txy(
            (PS2_ANALOG_STICK_WIDTH + PS2_ANALOG_STICK_HOLE_SPACING_Y) / 2,
            PS2_ANALOG_STICK_HOLE_OFFSET_X) hole();
        txy(
            (PS2_ANALOG_STICK_WIDTH - PS2_ANALOG_STICK_HOLE_SPACING_Y) / 2,
            PS2_ANALOG_STICK_HOLE_OFFSET_X + PS2_ANALOG_STICK_HOLE_SPACING_X
        ) hole();
        txy(
            (PS2_ANALOG_STICK_WIDTH + PS2_ANALOG_STICK_HOLE_SPACING_Y) / 2,
            PS2_ANALOG_STICK_HOLE_OFFSET_X + PS2_ANALOG_STICK_HOLE_SPACING_X
        ) hole();
      }

    }

    module motor_controller_cutout() {
      module corner() {
        corner_radius = 4;
        tz(-overlap) cylinder(
            r=corner_radius, control_box_base_to_pcb + overlap * 2);
      }
      tz(-MOTOR_CONTROLLER_PCB_HEIGHT - control_box_base_to_pcb - overlap)
        difference() {
          txy(-board_spacing, -board_spacing) cube([
              MOTOR_CONTROLLER_PCB_WIDTH + board_spacing * 2,
              MOTOR_CONTROLLER_PCB_LENGTH + board_spacing * 2,
              control_box_base_to_pcb + MOTOR_CONTROLLER_PCB_HEIGHT +
                  overlap * 2]);
          txy(-board_spacing, -board_spacing) difference() {
            cube([
                MOTOR_CONTROLLER_PCB_WIDTH + board_spacing * 2,
                MOTOR_CONTROLLER_PCB_LENGTH + board_spacing * 2,
                control_box_bottom_pad
            ]);
            translate([
                MOTOR_CONTROLLER_PCB_WIDTH / 2,
                MOTOR_CONTROLLER_PCB_LENGTH / 2,
                -overlap]) honeycomb([
                  MOTOR_CONTROLLER_PCB_WIDTH,
                  MOTOR_CONTROLLER_PCB_LENGTH * 1.5,
                  control_box_base_to_pcb], 5,
                  1);
          }
          corner();
          tx(MOTOR_CONTROLLER_PCB_WIDTH) corner();
          ty(MOTOR_CONTROLLER_PCB_LENGTH) corner();
          txy(MOTOR_CONTROLLER_PCB_WIDTH, MOTOR_CONTROLLER_PCB_LENGTH)
            corner();
        }
    }
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

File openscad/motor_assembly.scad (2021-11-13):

use <lib/mattwach/util.scad>
include <lib/mattwach/vitamins/bolts.scad>
include <pole_interface.scad>
include <motor_carriage.scad>
include <threaded_attachment.scad>

module motor_assembly() {
  connection_bolt_length = 20;
  module motor() {
    tz(MOTOR_LENGTH + GEAR_BOX_LENGTH + MOTOR_CARRIAGE_MOUNT_THICKNESS)
      rx(180) {
      motor_with_gearbox();
      tz(MOTOR_LENGTH + GEAR_BOX_LENGTH + MOTOR_CARRIAGE_MOUNT_THICKNESS) {
        ty(GEAR_BOX_SCREW_SPACING / 2) bolt_M2_5(10);
        ty(-GEAR_BOX_SCREW_SPACING / 2) bolt_M2_5(10);
      }
    }
  }

  module linkage_bolt() {
    translate(
        [-DISTANCE_FROM_AXIS_TO_HOLE,
        -connection_bolt_length / 2 + 1.5,
        CONNECTION_TAB_WIDTH / 2
    ]) rx(90) {
      bolt_M3(length=connection_bolt_length);
      tz(-(connection_bolt_length - 1)) nut_M3();
    }
  }

  module threaded_attachment_assembled() {
    tz(-THREADED_ATTACHMENT_LENGTH - FLANGE_HEIGHT - 2) {
      tz(THREADED_ATTACHMENT_LENGTH)
        flange_with_bolts(THREADED_ATTACHMENT_FLANGE_BOLT_LENGTH);
      threaded_attachment();  // Prefix a ! here to 3D print this part
    }
  }

  // Instructions: add a ! to print the part.  Example !motor_carriage()
  motor();
  color("red", 0.7) motor_carriage();  // Prefix a ! here to 3D print this part
  color("purple", 0.7) motor_carriage_cover();  // Prefix a ! here to 3D print this part
  color("green", 0.7) pole_interface();  // Prefix a ! here to 3D print this part
  linkage_bolt();
  threaded_attachment_assembled();
}

$fa = 2.0;
$fs = 0.5;
motor_assembly();

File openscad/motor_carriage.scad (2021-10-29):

use <lib/mattwach/util.scad>
include <lib/pole_threads.scad>
include <vitamins/motor_with_gearbox.scad>

CONNECTION_TAB_WIDTH = 18;
MOTOR_CARRIAGE_MOUNT_THICKNESS = 2;
MOTOR_CARRIAGE_HEIGHT = MOTOR_CARRIAGE_MOUNT_THICKNESS + MOTOR_AND_GEAR_BOX_LENGTH + 12;
MOTOR_CARRIAGE_HOLDER_PAD = 3;
MOTOR_CARRIAGE_DIAMETER = MOTOR_DIAMETER + MOTOR_CARRIAGE_HOLDER_PAD * 2;
MOTOR_SPACING = 0.2;
LINKAGE_TAB_EXTENSION = 10;
LINKAGE_TAB_WIDTH = 7;
SCREW_HOLE_PAD = 0.25;
DISTANCE_FROM_AXIS_TO_HOLE = GEAR_BOX_DIAMETER / 2 - MOTOR_CARRIAGE_MOUNT_THICKNESS / 2 + MOTOR_CARRIAGE_HOLDER_PAD + LINKAGE_TAB_EXTENSION;

module motor_carriage() {
  overlap = 0.01;
  module linkage_tabs() {
    module linkage_tab() {
      fillet = CONNECTION_TAB_WIDTH;
      tab_size = 6;

      module hole() {
        tz(-overlap) cylinder(d=3.25, h=LINKAGE_TAB_WIDTH + overlap * 2);
      }

      rx(90)
        difference() {
          tz(-LINKAGE_TAB_WIDTH / 2)
            hull() {
              tx(-tab_size) cube([tab_size, CONNECTION_TAB_WIDTH, LINKAGE_TAB_WIDTH]);
              txy(LINKAGE_TAB_EXTENSION, CONNECTION_TAB_WIDTH / 2) cylinder(d=fillet, h=LINKAGE_TAB_WIDTH);
            }
          translate([
              LINKAGE_TAB_EXTENSION,
              CONNECTION_TAB_WIDTH / 2,
              -LINKAGE_TAB_WIDTH / 2
          ]) hole();
        }
    }

    rz(180) difference() {
      tx(GEAR_BOX_DIAMETER / 2 + MOTOR_CARRIAGE_HOLDER_PAD - MOTOR_CARRIAGE_MOUNT_THICKNESS / 2)
        linkage_tab();
      tz(-overlap)
        cylinder(
            d=(MOTOR_CARRIAGE_DIAMETER + MOTOR_DIAMETER) / 2,
            h=CONNECTION_TAB_WIDTH + overlap * 2);
    }
  }

  module gear_box_carriage() {
    bushing_pad = 1;
    module gear_box_screw_hole() {
      tz(-overlap)
        cylinder(
            d=GEAR_BOX_SCREW_HOLE_DIAMETER + SCREW_HOLE_PAD * 2,
            h = MOTOR_CARRIAGE_MOUNT_THICKNESS + overlap * 2); 
    }

    module wire_slot() {
      wire_diameter = 5;
      rz(30)
        tyz(MOTOR_DIAMETER / 2, MOTOR_CARRIAGE_HEIGHT - wire_diameter + overlap)
        rx(-90) union() {
          cylinder(d=wire_diameter, h = MOTOR_CARRIAGE_HOLDER_PAD);
          txy(-wire_diameter / 2, -wire_diameter)
            cube([wire_diameter, wire_diameter, MOTOR_CARRIAGE_HOLDER_PAD]);
      }
    }

    module ziptie_ring() {
      ziptie_width = 2.5;
      indent = 1;
      offset = 15;

      outer_diameter = MOTOR_CARRIAGE_DIAMETER + overlap;
      inner_diameter = outer_diameter - indent * 2;

      tz(MOTOR_CARRIAGE_HEIGHT - ziptie_width - offset)
        difference() {
          cylinder(d=outer_diameter, h=ziptie_width);
          tz(-overlap) cylinder(d=inner_diameter, h=ziptie_width + overlap * 2);
        }
    }

    module cooling_slots() {
      slot_count = 8;
      module cooling_slot() {
        slot_width = 3;
        top_border = 22;
        bottom_border = 12;
        tyz(MOTOR_CARRIAGE_DIAMETER / 2, bottom_border)
        rx(90)
          hull() {
            cylinder(d=slot_width, h=MOTOR_CARRIAGE_DIAMETER / 2);
            ty(MOTOR_CARRIAGE_HEIGHT - top_border - bottom_border) cylinder(d=slot_width, h=MOTOR_CARRIAGE_DIAMETER / 2);
          }
      }

      for (i = [3:slot_count + 1]) {
        rz(i * 360 / slot_count) cooling_slot();
      }
    }

    difference() {
      cylinder(d = GEAR_BOX_DIAMETER + MOTOR_CARRIAGE_HOLDER_PAD * 2, h=MOTOR_CARRIAGE_HEIGHT);
      tz(MOTOR_CARRIAGE_MOUNT_THICKNESS)
        cylinder(d = MOTOR_DIAMETER + MOTOR_SPACING * 2, h=MOTOR_CARRIAGE_HEIGHT); 
      tz(-overlap)
        cylinder(d=MOTOR_BUSHING_DIAMETER + bushing_pad * 2, h=MOTOR_CARRIAGE_MOUNT_THICKNESS + overlap * 2);
      ty(GEAR_BOX_SCREW_SPACING / 2) gear_box_screw_hole();
      ty(-GEAR_BOX_SCREW_SPACING / 2) gear_box_screw_hole();
      wire_slot();
      ziptie_ring();
      cooling_slots();
    }
  }

  union() {
    gear_box_carriage();
    linkage_tabs();
  }
}

module motor_carriage_cover() {
  cover_thickness = 3;
  seal_overlap = 3;
  seal_thickness = 2.5;
  overlap = 0.01;
  seal_diameter = MOTOR_DIAMETER + MOTOR_SPACING * 2;
  tz(MOTOR_CARRIAGE_HEIGHT) {
    union() {
      cylinder(d=MOTOR_CARRIAGE_DIAMETER, h=cover_thickness);
      difference() {
        tz(-seal_overlap)
          cylinder(d=seal_diameter, h=seal_overlap + overlap);
        tz(-seal_overlap-overlap)
          cylinder(d=seal_diameter - seal_thickness * 2, h=seal_overlap + overlap);
      }
    }
  }
}

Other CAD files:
openscad/motor_controller_pcb.scad
openscad/main.scad
openscad/pole_interface.scad
openscad/threaded_attachment.scad
openscad/vitamins/flange.scad
openscad/vitamins/motor_with_gearbox.scad

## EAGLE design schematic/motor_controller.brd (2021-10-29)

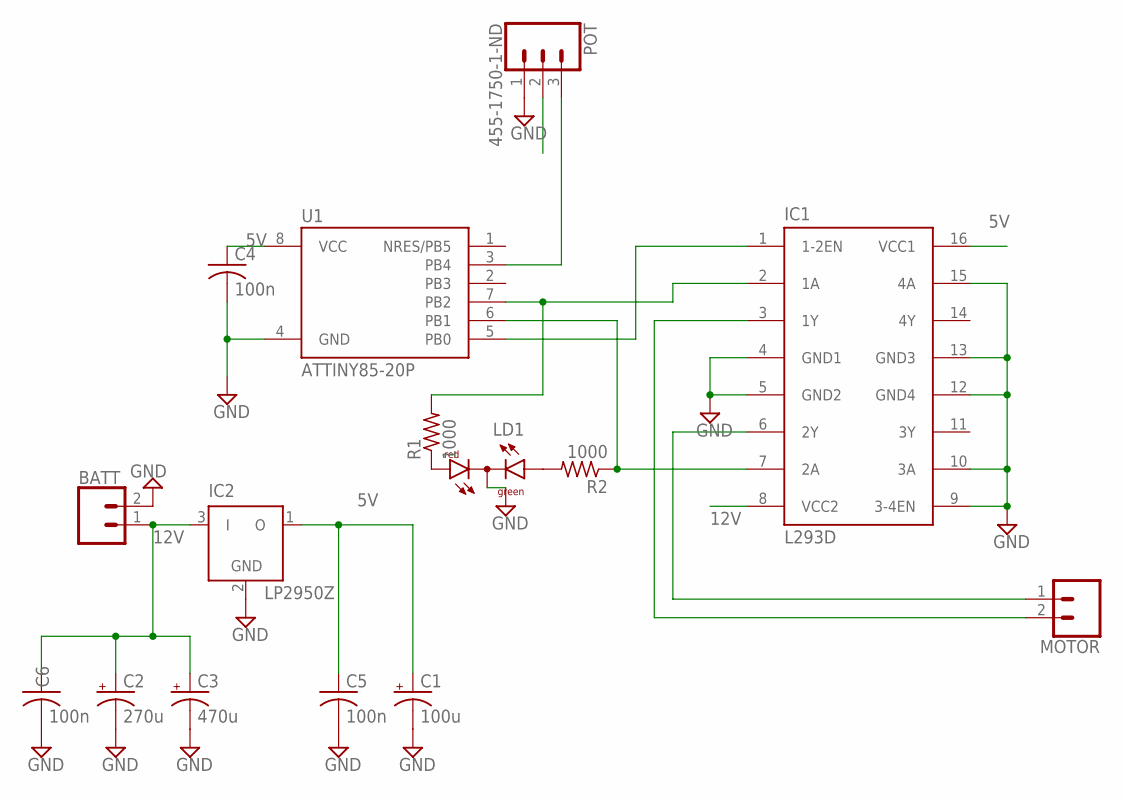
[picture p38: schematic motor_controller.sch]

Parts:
BATT: CONN_02; 1X02
C1: 100u; E3,5-10
C2: 270u; E3,5-10
C3: 470u; E3,5-10
C4, C5, C6: 100n; C050-055X075
IC1: L293D; DIL16
IC2: LP2950Z; TO92
LD1: DUOLED-RG-C; DUOLED-C-5MM
MOTOR: CONN_02; 1X02
POT: 455-1750-1-ND; 1X03
R1, R2: 1000; 0204/7
U1: ATTINY85-20P; PDIP08_300MIL

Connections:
5V: C1.+, C4.1, C5.1, IC1.16 (VCC1), IC2.1 (O), POT.2, U1.8 (VCC)
12V: BATT.1, C2.+, C3.+, C6.1, IC1.8 (VCC2), IC2.3 (I)
GND: BATT.2, C1.-, C2.-, C3.-, C4.2, C5.2, C6.2, IC1.4 (GND1), IC1.5 (GND2), IC1.9 (3-4EN), IC1.10 (3A), IC1.12 (GND4), IC1.13 (GND3), IC1.15 (4A), IC2.2 (GND), LD1.C, POT.1, U1.4 (GND)
unnamed: IC1.1 (1-2EN), U1.5 (PB0)
unnamed: IC1.6 (2Y), MOTOR.1
unnamed: IC1.3 (1Y), MOTOR.2
unnamed: IC1.7 (2A), R2.1, U1.6 (PB1)
unnamed: IC1.2 (1A), R1.2, U1.7 (PB2)
unnamed: LD1.AR, R1.1
unnamed: LD1.AX (AG), R2.2
unnamed: POT.3, U1.3 (PB4)

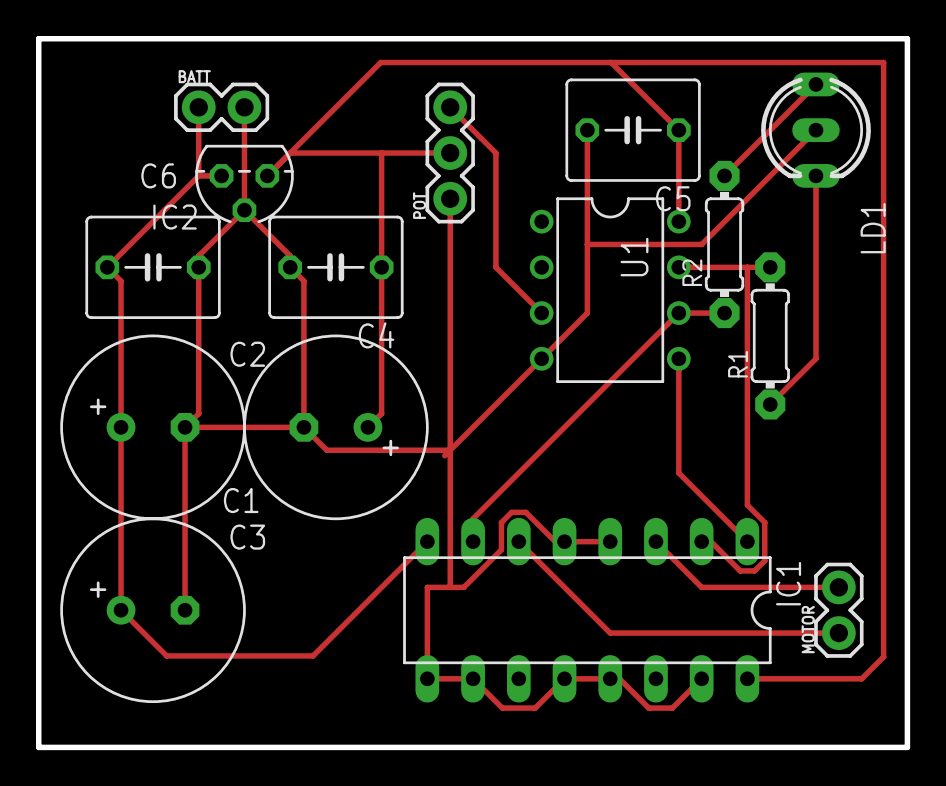
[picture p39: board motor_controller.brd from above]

Board: 2 copper layers, 48.3 x 39.4 mm, 15 parts (0 on the bottom side), 11 nets.

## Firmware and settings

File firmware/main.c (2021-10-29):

// Controls a FC motor via a L293D Hbridge and a potentiometer input.
//
// Hardwre:
//   Potentiometer (POT)
//   ATtiny85
//   L293D + DC motor 
// 
// Pin hookups:
//
//  N/C -+------+- VCC (5V)
//  N/C -|Tiny85|- REV
// ADC2 -|      |- FWD
//  GND -+------+- OC0A
//
//     ADC2
//       |
// VCC /\/\/ GND
//
// OC0A -+-----+- VCC (5V)
//  FWD -|L293D|- GND (Input)
// MOT1 -|     |- N/C (Output)
//  GND -|     |- GND
//  GND -|     |- GND
// MOT2 -|     |- N/C (Output)
//  REV -|     |- GND (Input)
//  12V -+-----+- GND (Enable 2)
//
// OC0A - PWM output
// FWD, REV: Motor enable and direction
// ADC2 - ADC Input

// How fast to loop
#define LOOP_DELAY_MS 50
// Deadband around the center
#define DEADBAND 12
// Minimum and maximum PWM output values (0-255)
#define MINIMUM_PWM 70
#define MAXIMUM_PWM 255
// Velocity says how it takes to go from zero to pull power (and visa versa).
// It's used to slow down the change rate.  This makes the system run more
// smoothly and is easier on the components.
#define RAIL_VELOCITY_MS 256

#include <adc/adc.h>
#include <util/delay.h>
#include <avr/io.h>

#define OC0A_PIN 0
#define FWD_PIN 1
#define REV_PIN 2
#define ADC_PIN 2  // ADC2, not comparable with other _PIN values

// We calculate the rail velocity period
// pwm_range = MAXIMUM_PWM - MINIMUM_PWM
// number_of_steps = RAIL_VELOCITY_MS / LOOP_DELAY_MS
//
// period = pwm_range / number_of_steps
//        = (MAXIMUM_PWM - MINIMUM_PWM) * LOOP_DELAY_MS / RAIL_VELOCITY_MS
//
// Example with: MINIMUM_PWM = 100, MAXIMUM_PWM = 200, LOOP_DELAY_MS = 50, RAIL_VELOCITY_MS = 500
//        = 100 * 50 / 500
//        = 5000 / 500
//        = 10 steps per period
//   at 10 steps per period, it will take 10 periods to cover 100.  10 periods happen in 500 ms.
//
// Same example with RAIL_VELOCITY_MS = 1000
//        = 100 * 50 / 1000
//        = 5000 / 1000
//        = 5 steps per period
#define RAIL_VELOCITY_PERIOD ((MAXIMUM_PWM - MINIMUM_PWM) * LOOP_DELAY_MS / RAIL_VELOCITY_MS)

static inline void disable_pwm() {
  // Turn off CS00, CS01, CS02.  Other bits can also be zero.
  TCCR0B = 0x00;
}

static inline void enable_pwm() {
  TCCR0B = 0x01; // Turns on clock with no prescaler
}

static inline void set_pwm_period(uint8_t period) {
  OCR0A = period;
}

static inline uint8_t pwm_period() {
  return OCR0A;
}

static inline uint8_t read_adc() {
  return adc_read8(ADC_PIN, ADC_REF_VCC, ADC_PRESCALER_128);
}

static void init() {
  // Set Inputs and Outputs
  DDRB = (1 << REV_PIN) | (1 << FWD_PIN) | (1 << OC0A_PIN);
  disable_pwm();

  // COM0A1 | COM0A0 == 0x80 => Clear on match, set on bottom
  // WGM00 | WGM01 == 0x03 => Fast PWM Mode
  TCCR0A = 0x83;
}

static inline uint8_t motor_is_running_forward() {
  return (PORTB & (1 << FWD_PIN)) != 0;
}

static inline uint8_t motor_is_running() {
  return (PORTB & ((1 << FWD_PIN) | (1 << REV_PIN))) != 0;
}

static void slow_down_or_stop_motor() {
  if (!motor_is_running()) {
    return;
  }

  const uint8_t current_pwm = pwm_period();
  if (current_pwm <= RAIL_VELOCITY_PERIOD) {
    // stop the motor
    PORTB &= ~((1 << FWD_PIN) | (1 << REV_PIN));
    disable_pwm();
    return;
  }

  // else, slow down the motor
  set_pwm_period(current_pwm - RAIL_VELOCITY_PERIOD);
}

static void start_motor(uint8_t is_forward_direction) {
  set_pwm_period(RAIL_VELOCITY_PERIOD);
  enable_pwm();
  if (is_forward_direction) {
    PORTB |= 1 << FWD_PIN;
  } else {
    PORTB |= 1 << REV_PIN;
  }
}

static void speed_up_motor(uint8_t target_pwm) {
  uint16_t new_pwm = (uint16_t)pwm_period() + RAIL_VELOCITY_PERIOD;
  if (new_pwm > (uint16_t)target_pwm) {
    // overshot the mark
    new_pwm = target_pwm;
  }
  set_pwm_period((uint8_t)new_pwm);
}

static void maybe_update_motor(uint8_t is_forward_direction, uint8_t target_pwm) {
  const uint8_t current_pwm = pwm_period();
  if (motor_is_running() &&
      (current_pwm > target_pwm || motor_is_running_forward() != is_forward_direction)) {
    slow_down_or_stop_motor();
    return;
  }

  if (target_pwm > 0 && !motor_is_running()) {
    start_motor(is_forward_direction);
    return;
  }

  if (current_pwm < target_pwm) {
    speed_up_motor(target_pwm);
  }

  // else current_pwn == target_pwm and the direction is correct so do nothing.
}

static void loop() {
  const uint8_t raw_adc_value = 255 - read_adc(); // reversed

  // determine forward or reverse
  const uint8_t is_forward_direction = (raw_adc_value >= 128);

  const uint8_t raw_magnitude = is_forward_direction ?
    raw_adc_value - 128 :  // forward
    128 - raw_adc_value;   // reverse

  uint8_t target_pwm = 0;
  if (raw_magnitude > DEADBAND) {
    const uint16_t magnitude = raw_magnitude - DEADBAND;

    // Convert magnitude to a target_pwm.
    // Some examples (DEADBAND=10, MINIMUM_PWM=100, MAXIMUM_PWM=200)
    // Lowest value:
    //   0 * 100 / 245 + 100 => 100
    // Highest Value:
    //   245 * 100 / 245 + 100 => 200
    // Halfway between:
    //   123 * 100 / 245 + 100 => 150 
    target_pwm = (uint8_t)(
        magnitude * (MAXIMUM_PWM - MINIMUM_PWM) /
        (128 - DEADBAND) + MINIMUM_PWM);
  }
  // else we are in the DEADBAND we we target zero (stop the motor)

  maybe_update_motor(is_forward_direction, target_pwm);
}

void main(void) {
  init();
  while (1) {
    loop();
    _delay_ms(LOOP_DELAY_MS);
  }
}

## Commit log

2021-10-29 Added firmware, 3d print files and schematics.
    [control_box_assembly.scad, flange.scad, main.scad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]
2021-11-09 Added wiring step
2021-11-13 Added 3D print instructions and STL models.
    [control_box_assembly.scad, control_box_bottom.stl, control_box_pole_interface.stl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]

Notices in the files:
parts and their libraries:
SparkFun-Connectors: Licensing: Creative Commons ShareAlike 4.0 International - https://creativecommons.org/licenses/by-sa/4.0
